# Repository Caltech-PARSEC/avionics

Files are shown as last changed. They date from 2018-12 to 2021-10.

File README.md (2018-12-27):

# Avionics

This repo is meant to contain the code for the microcontrollers on each board
and the Altium Designer files associated with the design of each board. When
adding your own stuff, try to stick with the folder naming convention and
structure seen here.

## Libraries
The libraries with the 'PARSEC' file name contain components that are generally
shared across the boards. If you need to add components for a project, add
them in a separate library file and add that file to the 'libraries' directory.

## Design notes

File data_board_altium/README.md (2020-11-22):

This folder is for Altium files for the on-rocket and ground station data boards.

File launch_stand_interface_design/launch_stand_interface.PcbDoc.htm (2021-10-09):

Reporting Options

# File in Previous Format

Date | : | 10/9/2021
Time | : | 3:20:03 PM
Filename | : | C:\Users\rayw1\Documents\GitHub\parsec_avionics\launch_stand_interface_design\launch_stand_interface.PcbDoc

Version | Warning

This file was generated by an earlier version of the software

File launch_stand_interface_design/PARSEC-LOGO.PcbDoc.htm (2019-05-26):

Reporting Options

# File in Previous Format

Date | : | 5/26/2019
Time | : | 2:11:39 AM
Filename | : | C:\Users\julli\OneDrive - California Institute of Technology\PARSEC\avionics\launch_stand_interface_design\PARSEC-LOGO.PcbDoc

Version | Warning

This file was generated by an earlier version of the software

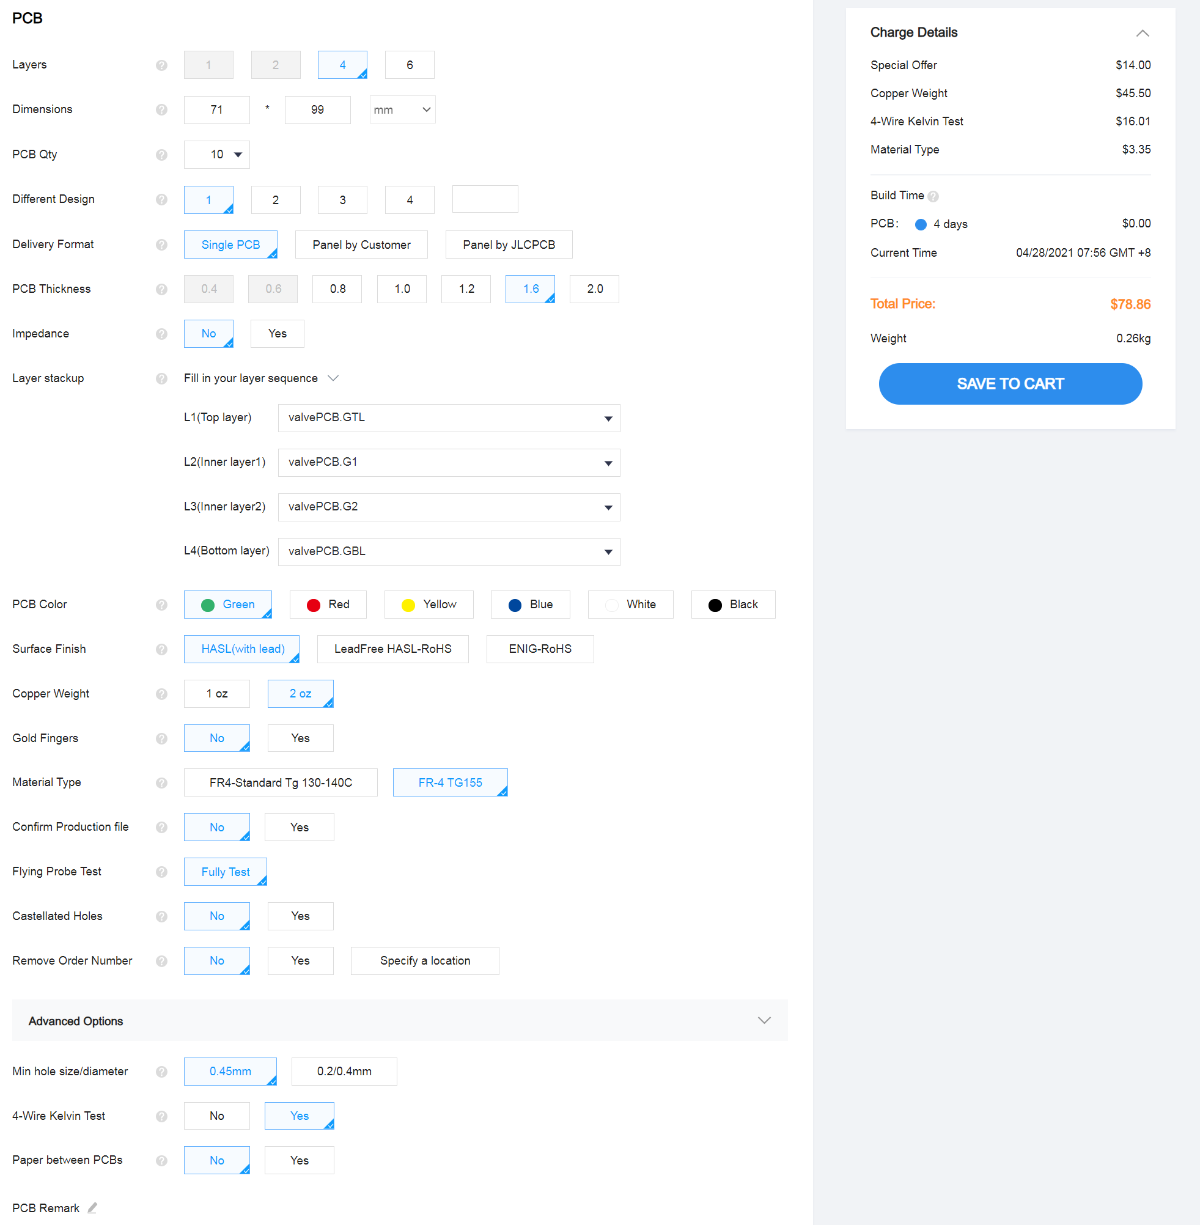
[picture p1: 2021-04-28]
valves/prop_valve_driver/valves_v2/JLCPCB_quote.PNG

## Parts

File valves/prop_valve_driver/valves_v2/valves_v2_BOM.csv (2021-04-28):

Comment | Description | Designator | Footprint | LibRef | Quantity | Value | Rating
CapCer | SMD Ceramic Capacitor | C1, C15, C16 | C0805_med_density | CapCer | 3 | 100n | 6.3V
CapTant | Through-hole tantalum capacitor | C2, C3, C4, C5 | C1206_tant_low_density | CapTant | 4 | 1u | 50V
CapCer | SMD Ceramic Capacitor | C6 | C0603_med_density | CapCer | 1 | 4u7 | 6.3V
CapCer | SMD Ceramic Capacitor | C7, C8, C10_FirstValve, C10_ThirdValve | C0603_med_density | CapCer | 4 | 100n | 6.3V
CapCer | SMD Ceramic Capacitor | C9 | C0603_med_density | CapCer | 1 | 10n | 6.3V
CapCer | SMD Ceramic Capacitor | C11, C12, C13, C14 | C0805_med_density | CapCer | 4 | 470n | 6.3V
CapCer | SMD Ceramic Capacitor | C17 | C0603_med_density | CapCer | 1 | 1u | 6.3V
1655-1921-1-ND | Schottky Diode | D1_FirstValve, D1_ThirdValve | DO-201AD | DiodeSchottky | 2
LED | Light-emitting diode | D2 | LED0805 | LED | 1 | Red
LED | Light-emitting diode | D3 | LED0805 | LED | 1 | Green
LED | Light-emitting diode | D4, D5 | LED0805 | LED | 2 | Blue
Molex KK 1x4 | 1x4 Molex KK Connector (CAN) | J1, J3 | Molex KK 4x1 | Molex KK 1x4 | 2
Battery | Molex 1x4 11A Connector | J2 | CON_2074781004_MOL | 2074781004 | 1
Header 4 | Header, 4-Pin | J4 | HDR1X4 | Header 4 | 1
Valve |  | J5_FirstValve, J5_ThirdValve | MOLEX_436500200 - duplicate | General Molex | 2
2STBN15D100 | 2STBN15D100 BJT | Q1_FirstValve, Q1_ThirdValve | D2PAK | BJT | 2
RK7002BMT116 | n-channel MOSEFT | Q2_FirstValve, Q2_ThirdValve | TRANS_RK7002BMHZG_ROM | RK7002BMT116 | 2
ResChip | SMD Chip resistor | R1 | R0805_med_density | ResChip | 1 | 120R
ResChip | SMD Chip resistor | R2 | R0805_med_density | ResChip | 1 | 100R
ResChip | SMD Chip resistor | R3_FirstValve, R3_ThirdValve | R1210_med_density | ResChip | 2 | 4m | 0.5W
ResChip | SMD Chip resistor | R4_FirstValve, R4_ThirdValve | R0603_med_density | ResChip | 2 | 91R | 0.25 W
ResChip | SMD Chip resistor | R5_FirstValve, R5_ThirdValve | R0603_med_density | ResChip | 2 | 10k
ResChip | SMD Chip resistor | R6_FirstValve, R6_ThirdValve | R0603_med_density | ResChip | 2 | 100R
ResChip | SMD Chip resistor | R7, R11 | R0805_med_density | ResChip | 2 | 240R
ResChip | SMD Chip resistor | R8 | R0805_med_density | ResChip | 1 | 412R
ResChip | SMD Chip resistor | R9, R15 | R0805_med_density | ResChip | 2 | 10R
ResChip | SMD Chip resistor | R12 | R0805_med_density | ResChip | 1 | 390R
ResChip | SMD Chip resistor | R13 | R0603_med_density | ResChip | 1 | 130R
ResChip | SMD Chip resistor | R14 | R0603_med_density | ResChip | 1 | 81R
ResChip | SMD Chip resistor | R16, R17, R18, R19 | R0805_med_density | ResChip | 4 | 100k
Switch | Push button switch, momentary, normally open | SW1, SW2, SW3, SW4, SW5 | PUSHBUTTON | Switch | 5
TCAN332DCNT | IC TXRX CAN 3.3V SOT23-8 | U1 | SOT-23-8 | TCAN332DCNT | 1
STM32F042K6T6 | STM32 MCU | U2 | LQFP-32 | STM32F042K6T6 | 1
INA240A3D | SchLib for TI op amp for current sensing. | U3_FirstValve, U3_ThirdValve | INA240A3D | INA240A3D | 2
LM317 | Linear Voltage Regulator | U4, U5 | D-PAK | LM317 | 2
SN74LVC14ADBR | Hex Schmitt-Trigger Inverter, DB0014A, LARGE T&R | U6 | SOP-14 | SN74LVC14 | 1 |  | Catalog
CSTCE8M00 | 8MHz Ceramic Resonator | Y1 | 8MHz Ceramic Resonator | CSTCE8M00 | 1

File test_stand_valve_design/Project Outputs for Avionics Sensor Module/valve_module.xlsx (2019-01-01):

Comment | Description | Designator | Footprint | LibRef | Quantity
1uF | 0805 Capacitor | C1, C22 | C0805 | C0805 | 2
0.1uF | 0805 Capacitor | C2, C23 | C0805 | C0805 | 2
100n | 0603 Capacitor | C3 | C0603 | C0603 | 1
1u | 0603 Capacitor | C4 | C0603 | C0603 | 1
100n | 0805 Capacitor | C5, C6, C7, C8, C10, C11, C12, C13, C14, C15, C16, C17 | C0805 | C0805 | 12
4u7 | 0805 Capacitor | C9 | C0805 | C0805 | 1
2u2 | 0603 Capacitor | C18, C19 | C0603 | C0603 | 2
1 uF | 0603 Capacitor | C20_VD1, C20_VD2, C20_VD3, C20_VD4, C20_VD5, C21_VD1, C21_VD2, C21_VD3, C21_VD4, C21_VD5 | C0603 | C0603 | 10
824501141 | TVS DIODE 14V 23.2V DO214AC | D1_VD1, D1_VD2, D1_VD3, D1_VD4, D1_VD5, D2_VD1, D2_VD2, D2_VD3, D2_VD4, D2_VD5 | DIODE-SMA | 824501141 | 10
LED | LED | D3 | 0805LED | LED | 1
FERRITE | FERRITE BEAD 0805 | FB1, FB2 | R0805 | FERRITE | 2
Molex KK 1x2 | 1x2 Molex KK Connector | P1, P2, P4_VD1, P4_VD2, P4_VD3, P4_VD4, P4_VD5, P5_VD1, P5_VD2, P5_VD3, P5_VD4, P5_VD5, P6 | Molex KK 2x1 | Molex KK 1x2 | 13
Molex KK 1x4 | 1x4 Molex KK Connector | P3, P7, P8, P9, P10, P11, P12, P13, P14, P15, P16 | Molex KK 4x1 | Molex KK 1x4 | 11
240R | RESISTOR 0805 | R1, R5 | R0805 | R0805 | 2
390R | RESISTOR 0805 | R2 | R0805 | R0805 | 1
100 | RESISTOR 0805 | R3 | R0805 | R0805 | 1
1k | RESISTOR 0805 | R4 | R0805 | R0805 | 1
536R | RESISTOR 0805 | R6 | R0805 | R0805 | 1
2k | RESISTOR 0805 | R7 | R0805 | R0805 | 1
Tactile Switch | TL3301AF160QG | SW1 | Tactile Switch | Tactile Switch | 1
LM317 | Linear Voltage Regulator | U1, U4 | D-PAK | LM317 | 2
MC-ARM-STM32F446-LQFP100 |  | U2 | STM-LQFP100_N | MC-ARM-STM32F446-LQFP100 | 1
 | Imported | U3_VD1, U3_VD2, U3_VD3, U3_VD4, U3_VD5 | PowerSO-20 | L298P013TR | 5
CSTCE8M00 | 8MHz Ceramic Resonator | Y1 | 8MHz Ceramic Resonator | CSTCE8M00 | 1

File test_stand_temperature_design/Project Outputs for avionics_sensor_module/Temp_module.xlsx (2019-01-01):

Comment | Description | Designator | Footprint | LibRef | Quantity
.1uF | 0805 Capacitor | C1 | C0805 | C0805 | 1
1uF | 0805 Capacitor | C2 | C0805 | C0805 | 1
100n | 0805 Capacitor | C3, C5, C6, C7, C8, C10, C11, C12, C13, C14, C15, C16, C17 | C0805 | C0805 | 13
1u | 0805 Capacitor | C4 | C0805 | C0805 | 1
4u7 | 0805 Capacitor | C9 | C0805 | C0805 | 1
2u2 | 0805 Capacitor | C18, C19 | C0805 | C0805 | 2
0.01uF | 0805 Capacitor | C20_TEMP1, C20_TEMP2, C20_TEMP3, C20_TEMP4, C20_TEMP5, C20_TEMP6, C20_TEMP7, C20_TEMP8, C20_TEMP9, C20_TEMP10, C22_TEMP1, C22_TEMP2, C22_TEMP3, C22_TEMP4, C22_TEMP5, C22_TEMP6, C22_TEMP7, C22_TEMP8, C22_TEMP9, C22_TEMP10 | C0805 | C0805 | 20
0.1uF | 0805 Capacitor | C21_TEMP1, C21_TEMP2, C21_TEMP3, C21_TEMP4, C21_TEMP5, C21_TEMP6, C21_TEMP7, C21_TEMP8, C21_TEMP9, C21_TEMP10, C23_TEMP1, C23_TEMP2, C23_TEMP3, C23_TEMP4, C23_TEMP5, C23_TEMP6, C23_TEMP7, C23_TEMP8, C23_TEMP9, C23_TEMP10, C24_TEMP1, C24_TEMP2, C24_TEMP3, C24_TEMP4, C24_TEMP5, C24_TEMP6, C24_TEMP7, C24_TEMP8, C24_TEMP9, C24_TEMP10 | C0805 | C0805 | 30
LED | LED | D1 | 0805LED | LED | 1
FERRITE | FERRITE BEAD 0805 | FB1, FB2 | R0805 | FERRITE | 2
PCC-SMP | THERMOCOUPLE CONNECTOR | J1_TEMP1, J1_TEMP2, J1_TEMP3, J1_TEMP4, J1_TEMP5, J1_TEMP6, J1_TEMP7, J1_TEMP8, J1_TEMP9, J1_TEMP10 | PCC-SMP | PCC-SMP | 10
Molex KK 1x2 | 1x2 Molex KK Connector | P1, P2 | Molex KK 2x1 | Molex KK 1x2 | 2
Header 4 | Header, 4-Pin | P3 | HDR1X4 | Header 4 | 1
240R | RESISTOR 0805 | R1 | R0805 | R0805 | 1
390 R | RESISTOR 0805 | R2 | R0805 | R0805 | 1
100R | RESISTOR 0805 | R3 | R0805 | R0805 | 1
1K | RESISTOR 0805 | R4 | R0805 | R0805 | 1
2k | RESISTOR 0805 | R5 | R0805 | R0805 | 1
Push Switch |  | SW1 | PUSHBUTTON | PUSHBUTTON | 1
LM317 | Linear Voltage Regulator | U1 | D-PAK | LM317 | 1
MC-ARM-STM32F446-LQFP100 |  | U2 | STM-LQFP100_N | MC-ARM-STM32F446-LQFP100 | 1
MAXIM TSSOP14 |  | U3_TEMP1, U3_TEMP2, U3_TEMP3, U3_TEMP4, U3_TEMP5, U3_TEMP6, U3_TEMP7, U3_TEMP8, U3_TEMP9, U3_TEMP10 | MAXIM TSSOP14 | MAXIM TSSOP14 | 10
CSTCE8M00 | 8MHz Ceramic Resonator | Y1 | 8MHz Ceramic Resonator | CSTCE8M00 | 1

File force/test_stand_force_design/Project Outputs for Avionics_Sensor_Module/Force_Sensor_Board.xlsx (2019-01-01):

Comment | Description | Designator | Footprint | LibRef | Quantity
0.1uF | 0805 Capacitor | C1, C5, C21_PA1, C21_PA2, C21_PA3 | C0805 | C0805 | 5
1uF | 0805 Capacitor | C2 | C0805 | C0805 | 1
100n | 0805 Capacitor | C3, C6, C7, C8, C9, C11, C12, C13, C14, C15, C16, C17, C18 | C0805 | C0805 | 13
1u | 0805 Capacitor | C4 | C0805 | C0805 | 1
4u7 | 0805 Capacitor | C10 | C0805 | C0805 | 1
 | 0805 Capacitor | C19, C20 | C0805 | C0805 | 2
BAT54-SOT23 | SINGLE SHOTTKY DIODE | D1_PA1, D1_PA2, D1_PA3 | SOT23-DIODE | BAT54-SOT23 | 3
LED | LED | D2 | 0805LED | LED | 1
FERRITE | FERRITE BEAD 0805 | FB1, FB2 | R0805 | FERRITE | 2
 | RESISTOR 0603 | Load_PA1, Load_PA2, Load_PA3 | R0603 | R0603 | 3
Molex KK 1x2 | 1x2 Molex KK Connector | P1, P2 | Molex KK 2x1 | Molex KK 1x2 | 2
Molex KK 1x4 | 1x4 Molex KK Connector | P3, P4, P5, P6, P8 | Molex KK 4x1 | Molex KK 1x4 | 5
Header 4 | Header, 4-Pin | P7 | HDR1X4 | Header 4 | 1
240R | RESISTOR 0805 | R1 | R0805 | R0805 | 1
5.6k | RESISTOR 0805 | R1_PA1, R1_PA2, R1_PA3 | R0805 | R0805 | 3
390R | RESISTOR 0805 | R2 | R0805 | R0805 | 1
1k | RESISTOR 0805 | R2_PA1, R2_PA2, R2_PA3, R5 | R0805 | R0805 | 4
120R | RESISTOR 0805 | R3 | R0805 | R0805 | 1
100R | RESISTOR 0805 | R4 | R0805 | R0805 | 1
10k | RESISTOR 0805 | R6_PA1, R6_PA2, R6_PA3 | R0805 | R0805 | 3
2k | RESISTOR 0805 | R7 | R0805 | R0805 | 1
1k3 | RESISTOR 0603 | Rg_PA1, Rg_PA2, Rg_PA3 | R0603 | R0603 | 3
Push Switch |  | SW1 | PUSHBUTTON | PUSHBUTTON | 1
LM317 | Linear Voltage Regulator | U1 | D-PAK | LM317 | 1
MC-ARM-STM32F446-LQFP100 |  | U2 | STM-LQFP100_N | MC-ARM-STM32F446-LQFP100 | 1
TCAN332DCNT | IC TXRX CAN 3.3V SOT23-8 | U3 | SOT-23-8 | TCAN332DCNT | 1
INA125_D_16 | Imported | U4_PA1, U4_PA2, U4_PA3 | D16 | INA125_D_16 | 3
CSTCE8M00 | 8MHz Ceramic Resonator | Y1 | 8MHz Ceramic Resonator | CSTCE8M00 | 1

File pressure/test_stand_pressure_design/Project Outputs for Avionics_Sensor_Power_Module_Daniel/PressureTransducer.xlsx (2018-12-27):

Comment | Description | Designator | Footprint | LibRef | Quantity
1.0uF | 0805 Capacitor | C1 | C0805 | C0805 | 1
0.1uF | 0805 Capacitor | C2 | C0805 | C0805 | 1
100n | 0805 Capacitor | C3, C4, C6, C7, C8, C9, C12, C13, C14, C15, C17, C18, C19, C20 | C0805 | C0805 | 14
1u | 0805 Capacitor | C5 | C0805 | C0805 | 1
4u7 | 0805 Capacitor | C10 | C0805 | C0805 | 1
2u2 | 0805 Capacitor | C11, C16 | C0805 | C0805 | 2
LED | LED | D1 | 0805LED | LED | 1
FERRITE | FERRITE BEAD 0805 | FB1, FB2 | R0805 | FERRITE | 2
Molex KK 1x2 | 1x2 Molex KK Connector | P1, P2 | Molex KK 2x1 | Molex KK 1x2 | 2
Molex KK 1x4 | 1x4 Molex KK Connector | P3, P4, P6_PT1, P6_PT2, P6_PT3, P6_PT4, P6_PT5, P6_PT6, P6_PT7, P6_PT8, P6_PT9 | Molex KK 4x1 | Molex KK 1x4 | 11
Header 4 | Header, 4-Pin | P5 | HDR1X4 | Header 4 | 1
240R | RESISTOR 0805 | R1, R6_PT1, R6_PT2, R6_PT3, R6_PT4, R6_PT5, R6_PT6, R6_PT7, R6_PT8, R6_PT9 | R0805 | R0805 | 10
390R | RESISTOR 0805 | R2 | R0805 | R0805 | 1
120R | RESISTOR 0805 | R3 | R0805 | R0805 | 1
100R | RESISTOR 0805 | R4 | R0805 | R0805 | 1
1k | RESISTOR 0805 | R5, R8 | R0805 | R0805 | 2
464R | RESISTOR 0805 | R7_PT1, R7_PT2, R7_PT3, R7_PT4, R7_PT5, R7_PT6, R7_PT7, R7_PT8, R7_PT9 | R0805 | R0805 | 9
Push Switch |  | SW1 | PUSHBUTTON | PUSHBUTTON | 1
LM317 | Linear Voltage Regulator | U1 | D-PAK | LM317 | 1
TCAN332DCNT | IC TXRX CAN 3.3V SOT23-8 | U2 | SOT-23-8 | TCAN332DCNT | 1
MC-ARM-STM32F446-LQFP100 |  | U3 | STM-LQFP100_N | MC-ARM-STM32F446-LQFP100 | 1
CSTCE8M00 | 8MHz Ceramic Resonator | Y1 | 8MHz Ceramic Resonator | CSTCE8M00 | 1

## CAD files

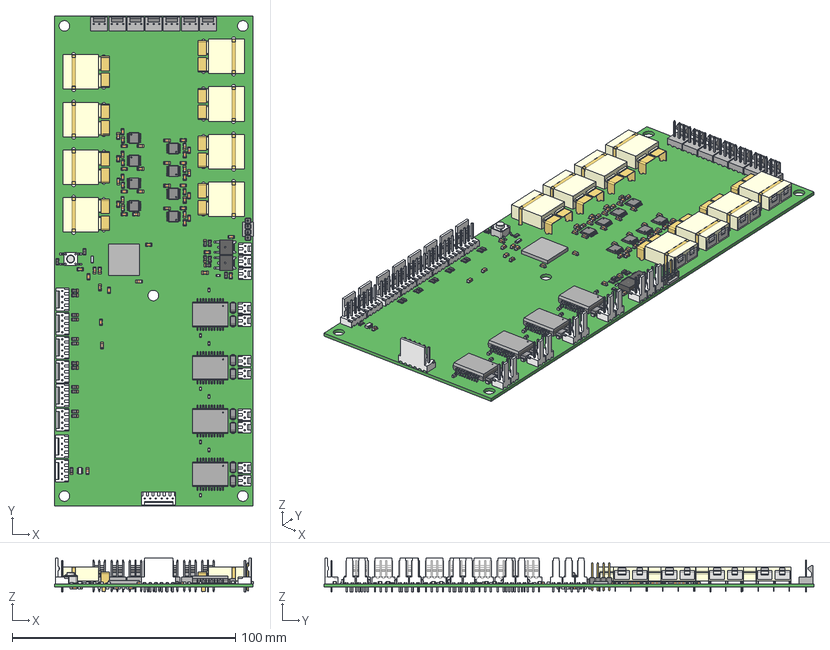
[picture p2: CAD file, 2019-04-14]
rocket_main/rocket_main.step
89.2 x 219.7 x 15.2 mm
Extruded x 30
User_Library-cap0805_pad_0805___ x 75
User_Library-cap0805_cap0805_body___ x 75
User_Library-Molex_-_3-Pin_Header_with_Lock_(0.100in_pitch)_Molex_-_ 3-Pin_Header_Base_with_Lock_(0.100in_pitch) x 7
User_Library-Molex_-_3-Pin_Header_with_Lock_(0.100in_pitch)_Molex_-_ Header_Pin x 21
User_Library-molex_kk_0_1in_latching_4_way_vertical_header x 8
User_Library-molex_kk_0_1in_latching_6_way_vertical_header
User_Library-TO252AA x 2
User_Library-res0805_pad_0805___ x 21
User_Library-res0805_res0805_body___ x 21
User_Library-molex_kk_0_1in_latching_2_way_vertical_header x 11
User_Library-LED_SMD0805
PowerSO-20 x 4
Thermocouple-PCC-SMP x 8
User_Library-DO-214Aa_SMA x 8
TSSOP14 x 8
CSTCE
User_Library-SOT23-8
TL1105CONTACTDOME
TL3301GBODY
TL1105COVER
TL1105-3301ACTUATOR_A_5

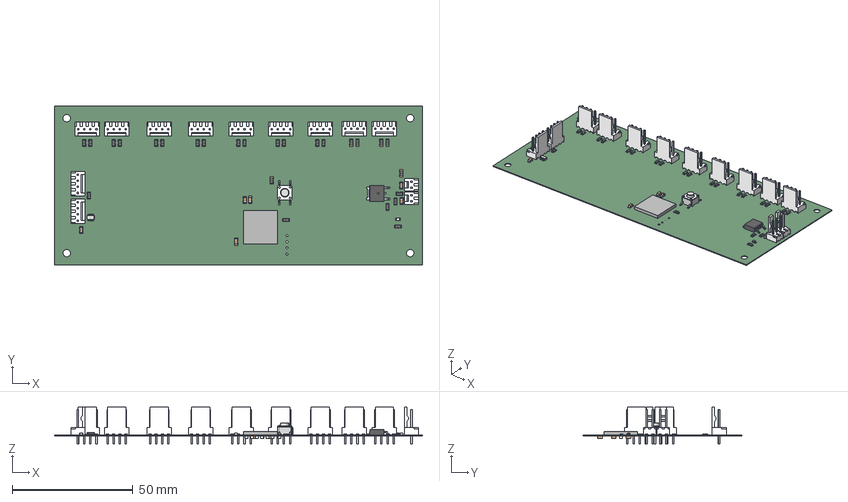
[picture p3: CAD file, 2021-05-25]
pressure/test_stand_pressure_design/PressureTransducer.step
152.4 x 65.9 x 15.2 mm
User_Library-res0805_pad_0805___ x 26
User_Library-res0805_res0805_body___ x 26
User_Library-LED_SMD0805
Extruded
User_Library-SOT23-8
User_Library-TO252AA
TL1105CONTACTDOME
TL3301GBODY
TL1105COVER
TL1105-3301ACTUATOR_A_5
User_Library-molex_kk_0_1in_latching_4_way_vertical_header x 11
User_Library-molex_kk_0_1in_latching_2_way_vertical_header x 2
User_Library-cap0805_pad_0805___ x 20
User_Library-cap0805_cap0805_body___ x 20

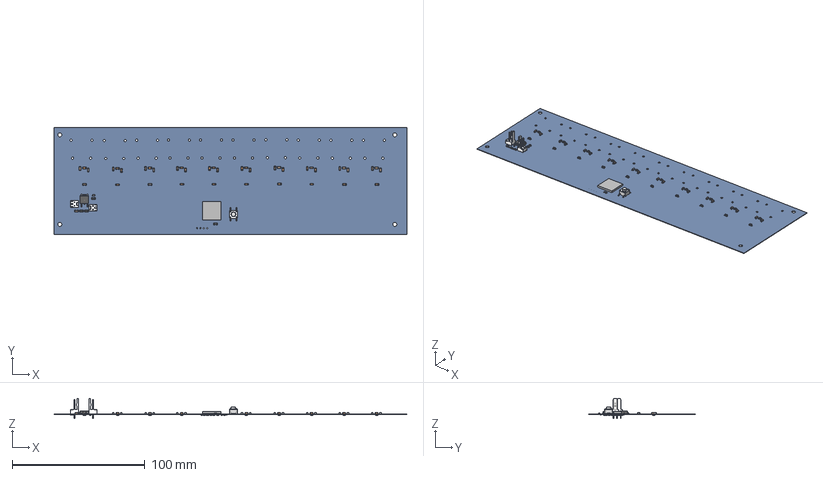
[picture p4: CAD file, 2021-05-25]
test_stand_temperature_design/Temp_module.step
266.1 x 80.4 x 15.2 mm
User_Library-res0805_pad_0805___ x 7
User_Library-res0805_res0805_body___ x 7
User_Library-LED_SMD0805
User_Library-cap0805_pad_0805___ x 69
User_Library-cap0805_cap0805_body___ x 69
User_Library-molex_kk_0_1in_latching_2_way_vertical_header x 2
User_Library-TO252AA
Extruded
TL1105CONTACTDOME
TL3301GBODY
TL1105COVER
TL1105-3301ACTUATOR_A_5

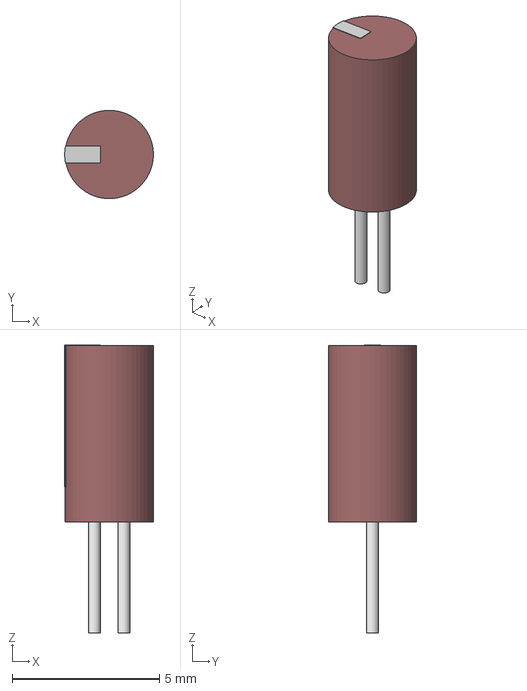
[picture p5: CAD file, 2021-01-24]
valves/prop_valve_driver/valves_v2/Models/CAP_UMA_3X5_NCH.step
3.01 x 3.00 x 9.77 mm

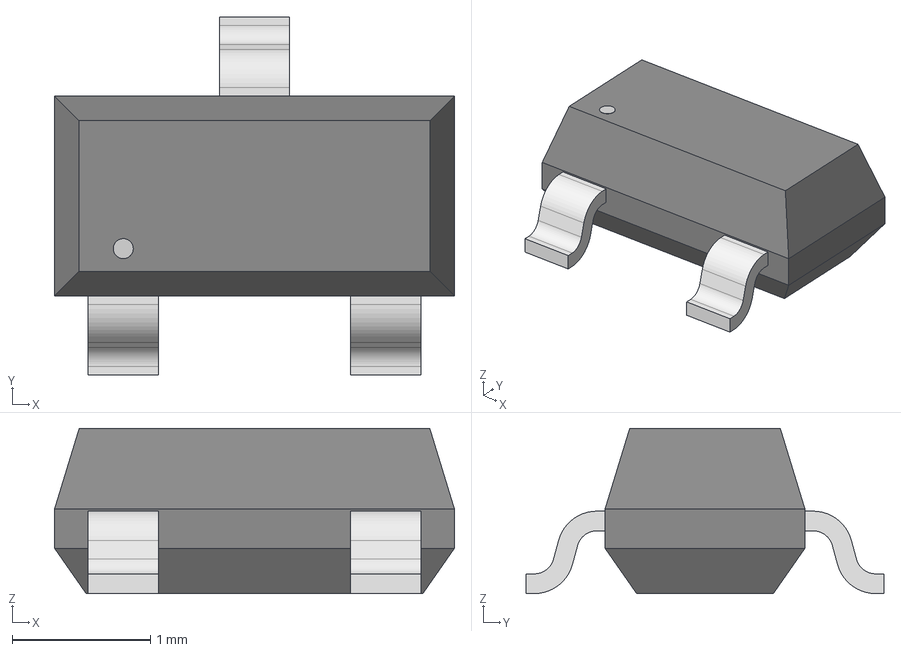
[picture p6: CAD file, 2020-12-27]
valves/prop_valve_driver/valves_v2/Models/TRANS_RK7002BMHZG_ROM.step
2.90 x 2.59 x 1.20 mm

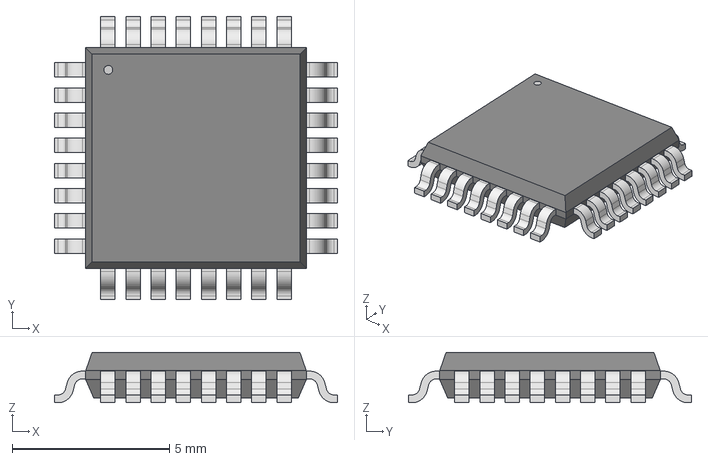
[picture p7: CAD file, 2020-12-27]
valves/prop_valve_driver/valves_v2/Models/LQFP-32.step
8.99 x 8.99 x 1.60 mm

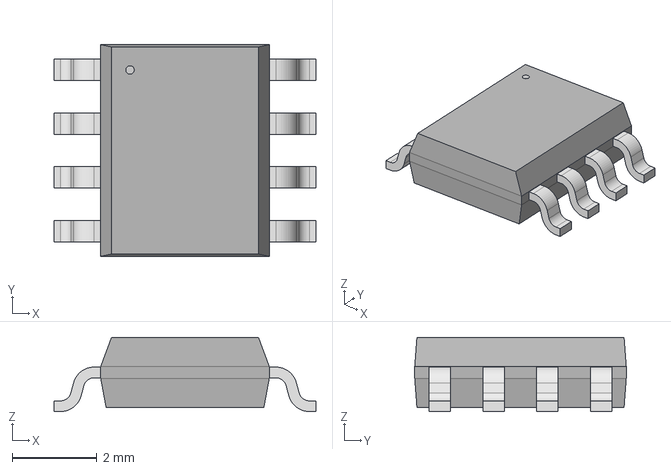
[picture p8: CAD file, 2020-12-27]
valves/prop_valve_driver/valves_v2/Models/D8_TEX-M.step
6.20 x 5.00 x 1.75 mm

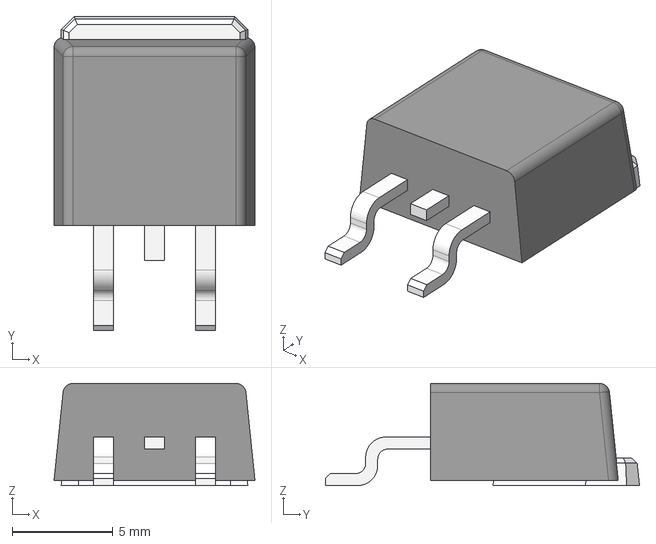
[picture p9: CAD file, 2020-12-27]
valves/prop_valve_driver/valves_v2/Models/D2PAK-2 L7805.step
10.0 x 15.6 x 5.08 mm

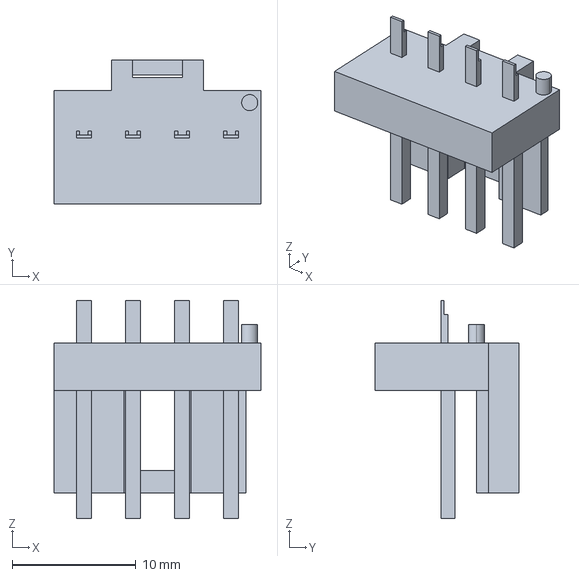
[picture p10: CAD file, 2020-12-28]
valves/prop_valve_driver/valves_v2/Models/2074781004.stp
16.7 x 11.6 x 17.6 mm

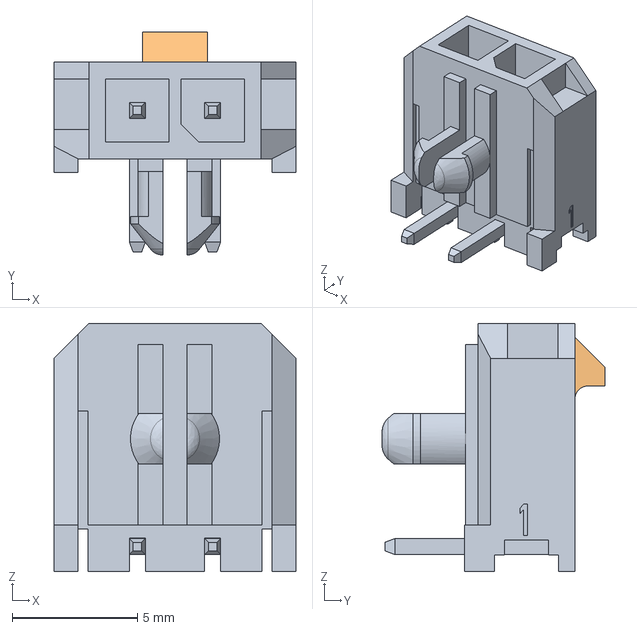
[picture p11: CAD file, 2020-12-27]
valves/prop_valve_driver/valves_v2/Models/436500200.stp
9.65 x 8.91 x 9.90 mm

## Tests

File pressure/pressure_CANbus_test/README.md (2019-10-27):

# Pressure CAN bus test
This code is designed to run a simple test of the ability of the pressure
boards to send and recieve CAN messages. When wired as described below,
pushing the button connected to one board will cause its LED to change, and
will cause it to send a CAN message to the other board instructing it to
set its LED to the opposite state of the original board's LED.

## Wiring
Pin header P6_PT9 connect to push button. Voltage should be normally 5V.
Pin header P6_PT5 connect to LED through ~100 ohm resistor.
The pin to use on each header is the one connected to R7_PTx.
Connect the CANH and CANL pins of the two pressure boards together.

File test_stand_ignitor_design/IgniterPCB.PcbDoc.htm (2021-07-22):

Reporting Options

# File in Previous Format

Date | : | 6/4/2021
Time | : | 3:36:19 AM
Filename | : | C:\Users\rayw1\Documents\GitHub\parsec_avionics\test_stand_ignitor_design\IgniterPCB.PcbDoc

Version | Warning

This file was generated by an earlier version of the software

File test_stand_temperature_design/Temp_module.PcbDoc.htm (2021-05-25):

Reporting Options

# File in Previous Format

Date | : | 5/25/2021
Time | : | 12:05:54 PM
Filename | : | C:\Users\julli\OneDrive - California Institute of Technology\PARSEC\avionics\test_stand_temperature_design\Temp_module.PcbDoc

Version | Warning

This file was generated by an earlier version of the software

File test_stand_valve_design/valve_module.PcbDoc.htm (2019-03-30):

Reporting Options

# File in Previous Format

Date | : | 3/29/2019
Time | : | 3:01:08 PM
Filename | : | C:\Users\julli\OneDrive - California Institute of Technology\PARSEC\avionics\test_stand_valve_design\valve_module.PcbDoc

Version | Warning

This file was generated by an earlier version of the software

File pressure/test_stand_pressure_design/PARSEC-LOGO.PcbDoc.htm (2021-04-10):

Reporting Options

# File in Previous Format

Date | : | 4/10/2021
Time | : | 6:36:28 PM
Filename | : | C:\Users\loren\Documents\Projects\PARSEC Electrical\avionics\pressure\test_stand_pressure_design\PARSEC-LOGO.PcbDoc

Version | Warning

This file was generated by an earlier version of the software

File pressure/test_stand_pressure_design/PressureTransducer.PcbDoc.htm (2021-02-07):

Reporting Options

# File in Previous Format

Date | : | 2/6/2021
Time | : | 9:37:24 PM
Filename | : | C:\Users\loren\Documents\Projects\PARSEC Electrical\avionics\pressure\test_stand_pressure_design\PressureTransducer.PcbDoc

Version | Warning

This file was generated by an earlier version of the software

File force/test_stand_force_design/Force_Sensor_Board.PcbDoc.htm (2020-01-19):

Reporting Options

# File in Previous Format

Date | : | 1/26/2019
Time | : | 7:23:34 PM
Filename | : | C:\Users\julli\OneDrive - California Institute of Technology\PARSEC\avionics\test_stand_force_design\Force_Sensor_Board.PcbDoc

Version | Warning

This file was generated by an earlier version of the software

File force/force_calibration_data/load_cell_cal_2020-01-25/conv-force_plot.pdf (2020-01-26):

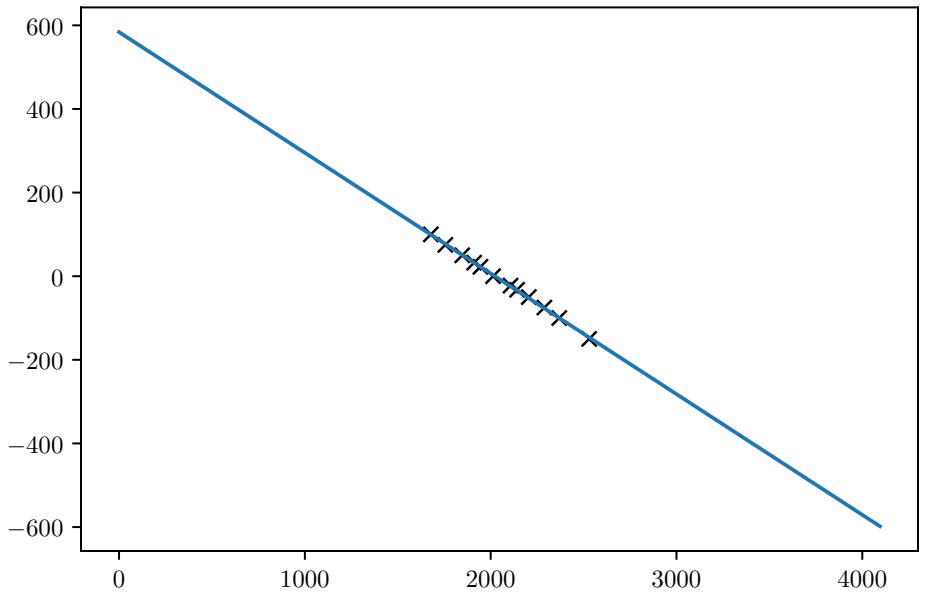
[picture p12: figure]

### ADC Conversion

### Pounds of compressive force

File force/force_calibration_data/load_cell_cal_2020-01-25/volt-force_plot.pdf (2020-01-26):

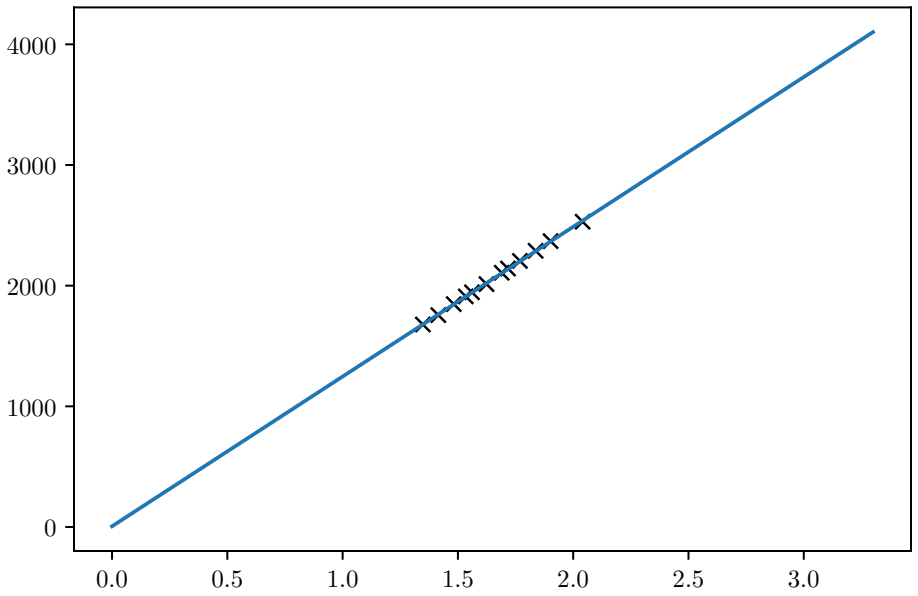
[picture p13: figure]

### Voltage (V)

### ADC Conversion value

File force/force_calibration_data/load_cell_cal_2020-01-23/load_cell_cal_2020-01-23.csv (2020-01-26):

Load Cell S/N | Port No. | Direction | Force (lbs) | ADC Conv.
1818000262 | 1 |  | 0 | 2041
1818000254 | 2 |  | 0 | 2018
1818000259 | 3 |  | 0 | 2041
1818000262 | 1 |  | 0 | 2033
1818000254 | 3 |  | 0 | 2031
1818000259 | 2 |  | 0 | 2030
1818000262 | 1 | Tension | 50 | 2045
1818000254 | 3 | Tension | 50 | 2192
1818000259 | 2 | Tension | 50 | 2202
1818000262 | 1 | Tension | 100 | 2066
1818000254 | 3 | Tension | 100 | 2367
1818000259 | 2 | Tension | 100 | 2378
1818000254 | 3 | Tension | 150 | 2544
1818000259 | 2 | Tension | 150 | 2532
1818000262 | 2 | Tension | 100 | 2374
1818000262 | 2 | Tension | 150 | 2530
1818000262 | 2 | Tension | 50 | 2195
1818000262 | 2 | Compression | 45 | 1959
1818000262 | 2 | Compression | 90 | 1959
1818000254 | 3 | Compression | 90 | 1965
1818000254 | 3 | Compression | 45 | 1963
1818000259 | 1 | Compression | 90 | 2011

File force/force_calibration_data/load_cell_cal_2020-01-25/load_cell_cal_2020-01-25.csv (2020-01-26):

Load Cell S/N | Port No. | Direction | Force (lbs) | ADC Conv. | Voltage (V)
1818000262 | 1 |  | 0 | 2013 | 1.624
1818000254 | 2 |  | 0 | 2002 | 1.62
1818000259 | 3 |  | 0 | 2044 | 1.646
1818000262 | 1 | Tension | 22.5 | 2107 | 1.69
1818000262 | 1 | Tension | 32.5 | 2142 | 1.717
1818000262 | 1 | Tension | 50 | 2205 | 1.769
1818000262 | 1 | Tension | 75 | 2289 | 1.837
1818000262 | 1 | Tension | 100 | 2369 | 1.902
1818000262 | 1 | Tension | 150 | 2530 | 2.041
1818000262 | 1 | Compression | 22.5 | 1945 | 1.561
1818000262 | 1 | Compression | 32.5 | 1911 | 1.534
1818000262 | 1 | Compression | 50 | 1847 | 1.482
1818000262 | 1 | Compression | 75 | 1756 | 1.415
1818000262 | 1 | Compression | 100 | 1678 | 1.348
1818000254 | 2 | Compression | 22.5 | 1923
1818000254 | 2 | Compression | 32.5 | 1900
1818000254 | 2 | Compression | 50 | 1827
1818000254 | 2 | Compression | 75 | 1749
1818000254 | 2 | Compression | 100 | 1661
1818000259 | 3 | Compression | 22.5 | 1963
1818000259 | 3 | Compression | 32.5 | 1921
1818000259 | 3 | Compression | 50 | 1869
1818000259 | 3 | Compression | 75 | 1774
1818000259 | 3 | Compression | 100 | 1687
1818000254 | 1 | Compression | 22.5 | 1918
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

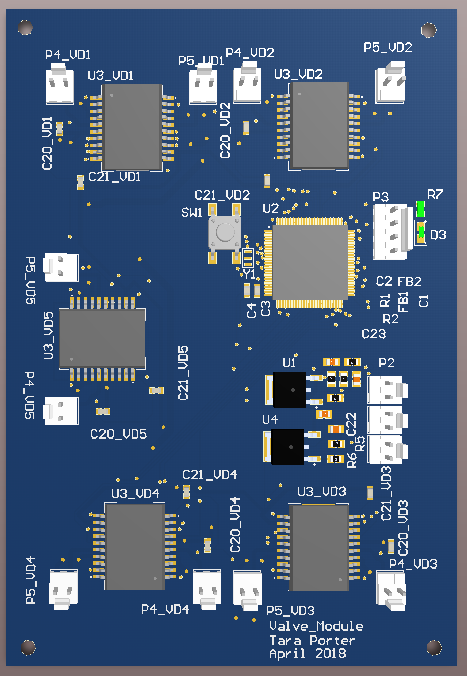
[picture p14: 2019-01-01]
test_stand_valve_design/valve pic.PNG

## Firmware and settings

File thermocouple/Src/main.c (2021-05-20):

/**
  ******************************************************************************
  * @file           : main.c
  * @brief          : Main program body
  ******************************************************************************
  ** This notice applies to any and all portions of this file
  * that are not between comment pairs USER CODE BEGIN and
  * USER CODE END. Other portions of this file, whether 
  * inserted by the user or by software development tools
  * are owned by their respective copyright owners.
  *
  * COPYRIGHT(c) 2021 STMicroelectronics
  *
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
  ******************************************************************************
  */
/* Includes ------------------------------------------------------------------*/
#include "main.h"
#include "stm32f4xx_hal.h"
#include "can.h"
#include "spi.h"
#include "tim.h"
#include "gpio.h"


/* USER CODE BEGIN PV */

/* USER CODE END PV */

void SystemClock_Config(void);

/* USER CODE BEGIN PFP */

/* USER CODE END PFP */

/* USER CODE BEGIN 0 */

// Structs for containing CAN message information
CAN_RxHeaderTypeDef baseCanRxHead;
CAN_TxHeaderTypeDef baseCanTxHead;

// The port number portion of the CAN ID corresponding to the message
// send for the data of each of the sensors, shifted so that the
// field is properly positioned within the CAN ID.
const int portNum[NUM_SENSORS] = {
    0 << PORT_NUM_SHIFT,
    1 << PORT_NUM_SHIFT,
    2 << PORT_NUM_SHIFT,
    3 << PORT_NUM_SHIFT,
    4 << PORT_NUM_SHIFT,
    5 << PORT_NUM_SHIFT,
    6 << PORT_NUM_SHIFT,
    7 << PORT_NUM_SHIFT,
    8 << PORT_NUM_SHIFT
};

// Expected to be used by the timer 3 ISR to determine which of the
// channels to average and send data for over the CAN bus.
//static int nextIdxToSend = 0;

// Chip select pins for each thermocouple
const uint16_t csPins[NUM_SENSORS] = {
  CS1_Pin, 
  CS2_Pin, 
  CS3_Pin, 
  CS4_Pin, 
  CS5_Pin, 
  CS6_Pin, 
  CS7_Pin, 
  CS8_Pin, 
  CS9_Pin, 
  CS10_Pin
};

// GPIO Port of each chip select pin
static GPIO_TypeDef* csPinPorts[NUM_SENSORS] = {
  CS1_GPIO_Port,
  CS2_GPIO_Port,
  CS3_GPIO_Port,
  CS4_GPIO_Port,
  CS5_GPIO_Port,
  CS6_GPIO_Port,
  CS7_GPIO_Port,
  CS8_GPIO_Port,
  CS9_GPIO_Port,
  CS10_GPIO_Port
};

// Buffer for each thermocouple's 3 byte reading
static uint8_t tempDataBuffer[NUM_SENSORS][3];
static uint8_t cjDataBuffer[2];
//static int tempDataReady[NUM_SENSORS] = {0, 0, 0, 0, 0, 0, 0, 0, 0, 0};


static uint8_t tempDataAddr[] = {0x0C};
static uint8_t cjDataAddr[] = {0x0A};
static uint8_t requestConv[2] = {0x80, 0b01000000};

// The number of thermocouple conversions triggered in
// the time it takes for a single conversion to complete.
// For a 660ms max conversion time, if we trigger a conversion
// every 100 ms, this value is ceiling(6.6) = 7
static int trigToReadGap = 7;

int trigInd = 0;
int readInd;

/* USER CODE END 0 */

/**
  * @brief  The application entry point.
  *
  * @retval None
  */
int main(void)
{
  /* MCU Configuration----------------------------------------------------------*/

  /* Reset of all peripherals, Initializes the Flash interface and the Systick. */
  HAL_Init();

  /* Configure the system clock */
  SystemClock_Config();

  /* Initialize all configured peripherals */
  MX_GPIO_Init();
  MX_CAN1_Init();
  MX_SPI1_Init();
  MX_TIM3_Init();

  /* USER CODE BEGIN 2 */
  // Start the IRQ timer on which data is sent over CAN
  HAL_TIM_Base_Start_IT(&htim3);


  // Initialize the CAN peripheral
  HAL_CAN_Init(&hcan1);

  // Configure CAN hardware receive filters
  //CAN_filterConfig();

  // Start the CAN module
  HAL_CAN_Start(&hcan1);


  // Start listening for CAN traffic on interrupt
  HAL_CAN_ActivateNotification(&hcan1, CAN_IT_RX_FIFO0_MSG_PENDING);

  // Set transmission parameters that are common to all Tx messages
  baseCanTxHead.IDE = CAN_ID_STD; // Standard 11-bit ID
  baseCanTxHead.StdId = OWN_CAN_ID; // CAN ID with port number = 0
  baseCanTxHead.RTR = CAN_RTR_DATA; // data frame (not a request frame)
  baseCanTxHead.DLC = 3;      // Number of data bytes


  // Just a buffer where AddTxMessage can return a code for which Tx
  // mailbox it added the message to. We don't care what it is.
  uint32_t mailbox;

  // Write all chip select pins low (inactive)
  for (int i = 0; i < NUM_SENSORS; i++)
  {
	  HAL_GPIO_WritePin(csPinPorts[i], csPins[i], 1);
  }

  // Initialize thermocouple signal processing ICs
  for (int i = 0; i < NUM_SENSORS; i++)
  {
	  // Write to configuration register 1 to average 16 samples per conversion,
	  // and ensure type K thermocouples are used.
	  uint8_t config1[2] = {0x81, 0b01110011};
	  HAL_GPIO_WritePin(csPinPorts[i], csPins[i], 0);
	  HAL_SPI_Transmit(&hspi1, (uint8_t *)config1, 2, HAL_MAX_DELAY);
	  HAL_GPIO_WritePin(csPinPorts[i], csPins[i], 1);
  }


  /* USER CODE END 2 */

  /* Infinite loop */
  /* USER CODE BEGIN WHILE */
  while (1)
  {

  /* USER CODE END WHILE */

  /* USER CODE BEGIN 3 */

  // Trigger a one-shot conversion to thermocouple number `trigInd`
  HAL_GPIO_WritePin(csPinPorts[trigInd], csPins[trigInd], 0);
  HAL_SPI_Transmit(&hspi1, (uint8_t *) requestConv, 2, HAL_MAX_DELAY);
  HAL_GPIO_WritePin(csPinPorts[trigInd], csPins[trigInd], 1);

  // Read the value from a previously triggered conversion on a
  // different thermocouple.
  readInd = (trigInd - trigToReadGap) % NUM_SENSORS;
  if (readInd < 0) {readInd += NUM_SENSORS;}

  HAL_GPIO_WritePin(csPinPorts[readInd], csPins[readInd], 0);
  HAL_SPI_Transmit(&hspi1, (uint8_t *) tempDataAddr, 1, HAL_MAX_DELAY);
  HAL_SPI_Receive(&hspi1, &tempDataBuffer[readInd][0], 3, HAL_MAX_DELAY);
  HAL_GPIO_WritePin(csPinPorts[readInd], csPins[readInd], 1);

  HAL_Delay(10);

  // For debugging, check what it's reading for cold junction temperature
  HAL_GPIO_WritePin(csPinPorts[readInd], csPins[readInd], 0);
  HAL_SPI_Transmit(&hspi1, (uint8_t *) cjDataAddr, 1, HAL_MAX_DELAY);
  HAL_SPI_Receive(&hspi1, (uint8_t *) cjDataBuffer, 2, HAL_MAX_DELAY);
  HAL_GPIO_WritePin(csPinPorts[readInd], csPins[readInd], 1);

  trigInd = (trigInd + 1) % NUM_SENSORS;


  int temp24 = tempDataBuffer[readInd][0] << 16 | \
                   tempDataBuffer[readInd][1] << 8 |  \
                   tempDataBuffer[readInd][2];

  int cjTemp = (cjDataBuffer[0] << 8) | cjDataBuffer[1];
  cjTemp = cjTemp & 0xFFFFFFFF;

//  if (temp24 & 0x800000)
//  {
//    temp24 |= 0xFF000000; //fix sign
//  }
//
//  temp24 >>= 5;
//
//  float tempfloat = temp24;
//  tempfloat *= 0.0078125;
//  tempfloat += 273.15;

  // Specify the contents of the message we're going to send.

  // Copy the base Tx message header into the header for this
  // message specifically.
  CAN_TxHeaderTypeDef msgCanTxHead =  baseCanTxHead;

  // Write the port ID for this sensor to the appropriate field
  // of the CAN ID.
  msgCanTxHead.StdId = OWN_CAN_ID | portNum[readInd];

  // Send the value for this sensor measurement over the CAN bus
  uint8_t canData[3];
  canData[2] = (temp24 >> 16) & 0xFF;
  canData[1] = (temp24 >> 8)  & 0xFF;
  canData[0] = temp24 & 0xFF;

  HAL_CAN_AddTxMessage(&hcan1, &msgCanTxHead, canData, &mailbox);

  HAL_Delay(100);


//  int sensorNum = 1;
///*    uint16_t msgID = create_ID(BOARD_ID, sensorNum);
//    can_msg_t msg;
//
//*/
//    uint16_t value = tempfloat*32;
///*    CAN_short_msg(&msg, msgID, value);
//
//    while(!CAN_can_transmit()){};
//
//    CAN_queue_transmit(&msg);
//
//*/
//    volatile int var = 0;
//
//  }
//  /* USER CODE END 3 */

  }
}

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


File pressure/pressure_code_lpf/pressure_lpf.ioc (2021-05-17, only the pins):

Mcu.UserName=STM32F446VETx
PA0-WKUP.Signal=ADCx_IN0
PA1.Signal=ADCx_IN1
PA11.Signal=CAN1_RX
PA12.Signal=CAN1_TX
PA13.Signal=SYS_JTMS-SWDIO
PA14.Signal=SYS_JTCK-SWCLK
PA2.Signal=ADCx_IN2
PA6.Signal=ADCx_IN6
PA7.Signal=ADCx_IN7
PC0.Signal=ADCx_IN10
PC1.Signal=ADCx_IN11
PC2.Signal=ADCx_IN12
PC4.Signal=ADCx_IN14
PH0-OSC_IN.Signal=RCC_OSC_IN
PH1-OSC_OUT.Signal=RCC_OSC_OUT

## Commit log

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2019-01-01 Added temperature sensor design and code and force sensor design.
    [Avionics_Sensor_Module.PrjPcb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]
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2019-02-09 Minor edits while looking around designs. The force code now records ADC status in a variable.
    [Avionics Sensor Module.PrjPcb, Force_Sensor_Board.PcbDoc, PressureTransducer.PcbDoc]
2019-02-15 The igniter board is now shrunk down to about 2.5 x 3 inches and all the design violations have been addressed. Also changed a parameter in the adc.c file of the force code to have NbrOfDiscConversio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
    [Force_Sensor_Board.PcbDoc, IgniterPCB.PcbDoc, igniter.PrjPcb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]
2019-03-26 main avionics pcb design
    laid out and routed everything for the rocket avionics board except IMU
    connector
    [Power.SchDoc, Power_Schematic.SchDoc, Pressure_Transducer.SchDoc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]
2019-03-27 Completed avionics board design
    Added CAN and IMU connectors, placed component labels, added mounting
    holes
    [imu.SchDoc, rocket_main.PcbDoc, rocket_main.PrjPcb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]
2019-03-28 Updated avionics board
    Added potentiometer connectors, caps on analog lines, and moved CAN chip
    [Power_Schematic.SchDoc, Pressure_Transducer.SchDoc, imu.SchDoc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]
2019-03-28 Converted board to 4 layers
    ground plane moved to 2nd layer, power traces moved to 3rd layer
    [Power_Schematic.SchDoc, Pressure_Transducer.SchDoc, Temp_converter.SchDoc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]
2019-03-29 changed STM coupling capacitors
    moved capacitors directly under STM32 and made connections from VDD pins
    to caps more direct; moved signals that were in the way
    [rocket_main.PcbDoc]
2019-03-29 fixed missing 12V connection
    [rocket_main.PcbDoc]
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2019-03-30 Revert "Messing about with the force board schematics"
    This reverts commit 2567c6b501821507388e7e40463a2e3277f00319.
2019-03-30 Fixed grounding issue with the force board
    [Force_Sensor_Board.PcbDoc, micro_schematic.SchDoc, power_amp_module.SchDoc]
2019-03-30 Added in an annotation file the last commit didn't catch.
    [Avionics_Sensor_Module.PrjPcb, Force_Sensor_Board.PcbDoc]
2019-03-30 Adding 3D models and DRC
    Added models for the thermocouple connectors and the ceramic resonator in the main board's libraries. Couldn't find a footprint for the thermocouple ICs in any libraries, so holding off on that for now. Also fixed some design rule violations (there were some traces from different nets running over each other near the top left TC connector and I relaxed some of the restrictions on pad/trace proximity (not sure if that's user or project based though - I suck at Altium).
    [rocket_main.PcbDoc]
2019-03-31 Updated TSSOP14 footprint
    Corrected the width of the MAXIM-TSSOP14 footprint for the thermocouple chips and added an outline and pad 1 indicator to it. Rerouted stuff as necessary and also cleaned up some traces coming off the microcontroller with the updated design rule.
    [Temp_converter.SchDoc, rocket_main.PcbDoc, rocket_main.PrjPcb]
2019-03-31 Added TSSOP14 3D Model. Also automatic library removal
    Altium gave me a "PARSEC.[xxx]Lib could not be found and was removed from the project", but it looks like it's still there and everything still seems fine.
    [rocket_main.PcbDoc, rocket_main.PrjPcb]
2019-03-31 TSSOP14 Footprint fix from last commit. Ran DRC
    In the previous commit, I set the origin reference of the TSSOP14 part to "center" and forgot to change it back to its original position. That is fixed now. I also ran DRC and removed some antenna traces (they were just little unconnected stubs) and relaxed some of the rules regarding silkscreen clearances. Not all the rules are resolved, but what's left is probably going to end up being waived, but I want to look through them all anyway. Mostly silk to silk clearance issues in the TC part of the board, but for most of them it's fine if some of the silk gets mushed together.
    [rocket_main.PcbDoc]
2019-04-03 added mounting hole
    added 5th mounting hole (also 6-32) in the middle of the board (x=1.75", y=3.8")
    [rocket_main.PcbDoc]
2019-04-04 Grounded mounting holes. Fixed missing connections
    The mounting holes were grounded because the screws going through them will be going directly into an aluminum box that will shield them from the radio beacon inside the rocket, and that shield needs to be grounded.
    The missing connections I found were two ground pins on the microcontroller and one ground pin on one of the thermocouple ICs that were not connected to ground. Fixed that now.
    [rocket_main.PcbDoc, rocket_main.PrjPcb]
2019-04-05 Added a 3D step file to top directory
    [rocket_main.step]
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2019-04-13 Labelled the CANH and CANL nets appropriately on Force board
    [Force_Sensor_Board.PcbDoc, micro_schematic.SchDoc]
2019-04-13 Shifted traces to make more room around mounting holes on rocket board
    Just making sure that traces don't get squashed by a screw.
    [rocket_main.PcbDoc]
2019-04-14 Enlarged mounting hole size and made room for it
    Mounting holes are now 3/8" diameter. Changed pot pins to 3x1 headers to make room for them, and moved some traces around in the bottom left of the board.
    [rocket_main.PcbDoc]
2019-04-14 Updated step file export
    Now has the 4x1 breakaway debugger pins modelled, and the mounting hole changes.
    [rocket_main.step]
2019-04-15 Silkscreen fixes
    Added Altium logo silkscreen, moved a few labels which were on top of vias for no reason.
    [altiumlogo.PcbDoc, rocket_main.PcbDoc, rocket_main.PrjPcb]
2019-04-15 Updated layer stack
    The PCB layers stack now conforms to the 1.6 mm stackup for JLCPCB, and the stackup files for JLCPCB were added to the top level directory.
    [rocket_main.PcbDoc]
2019-04-16 Ran a final DRC and generated fabrication outputs
    [rocket_main.GBL, rocket_main.GBO, rocket_main.GBS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]
2019-04-16 Added keepout layer and moved comonents in from edge
    Keepout layer provides and outline of the board (needed for fabrication by JLCPCB). This prevents copper from being placed near the edges as well. Thus, I needed to move some things in from the edges and reroute some things accordingly. Fixed DRC violations from this process.
    [rocket_main.PcbDoc]
2019-04-17 Updated fabircation outputs with changes of previous commit
    [rocket_main.GBL, rocket_main.GBS, rocket_main.GKO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]
2019-04-17 Added folder with only files to be sent to JLCPCB for fabrication.
    [rocket_main.GBL, rocket_main.GBO, rocket_main.GBS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]
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2019-04-24 Implemented David and Tyler's final revisions
    Added 45 uF of bulk storage capacitors to LM317s and 15 uF to each valve driver IC to keep the 12V line from dipping when valves draw lots of power.
    Added pull-down resistors to each used enable line for the valve drivers to prevent the line from going high during MCU booting.
    Increased by 10x the resistor values of R6 and R7 (the divider on pressure transducer output) to reduce load on the transducers and be more power efficient.
    Added connector for UART.
    Increased copper pad area and added thermal vias to the LM317 ICs. Complemented this by making the power rails transmitted by copper polygons, for the most part. Also added bottom coppe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
    [Power.SchDoc, Power_Schematic.SchDoc, PressureTransducer.PcbDoc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]
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2019-05-13 finished interface board
    added ignitor connections and cleaned up labels
    [launch_stand_interface.PcbDoc, launch_stand_interface.SchDoc]
2019-05-26 updated interface board for new power supply
    switched from 24pin atx connector to 4pin
    [launch_stand_interface.PcbDoc, launch_stand_interface.PrjPcb, launch_stand_interface.SchDoc]
2019-05-26 Made interface board better suited to high currents
    Replaced backup KK connectors with big pads to solder wires onto. Replaced 12V power traces with polygons, since the 30 mil traces wouldn't be able to handle the expected current draw of all the launch stand boards. Have yet to add some KK connectors to accomodate potential extra boards. The input pads could also have their shape tweaked.
    [launch_stand_interface.PcbDoc, launch_stand_interface.PrjPcb]
2019-05-26 Final edits and fabrication outputs for interface board.
    [PARSEC-LOGO.PcbDoc, altiumlogo.PcbDoc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]
2019-06-17 Corrected labels on ignitor output pins.
    [launch_stand_interface.PcbDoc, launch_stand_interface.PrjPcb]
2019-09-11 Updated CAN configs in pressure code
    CAN bus now runs at 500 kb/s baud with a bit sample point at 86.7%. This should make the bus more tolerant of bit timing errors, which is important with both the beaglebone and stm32s as CAN controllers on the same network
    [can.c]
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2020-01-12 Stuck old code into an archive folder
    [Avionics_Forse_Sensor_Program.ioc, PARSEC_Pressure.ioc, can.c]
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2020-01-23 Preparations for load cell calibration
    Wrote code for calibrating load cells, and got a csv ready and documented for taking data.
    [lm317_10V_2018PCB_load_cell_calibration.csv]
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2020-11-23 Added schematics and parts for in flight data
    Added SMT Microcontroller CAD (schematic and PCB) to Altium library. Also added 3V3 and CAN bus to newly created github project for the in flight data board.
    [CAN_circuit.SchDoc, Power_Schematic.SchDoc, flight_data_rocket_board.PrjPcb]
2020-12-20 Updated libraries with pcb and sch files for FT230XS chip
    *Note: I think I may have accidentally added the pcb file twice to the PARSEC library since the first time I copy/pasted the component it didn't copy anything for some reason. I wasn't sure if I should delete the empty file, so I have left it in the pcb library.
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2021-01-24 Added power bypass capacitors and fixed footprints
    [Power.SchDoc, ValveControl.SchDoc, valvePCB.PcbDoc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]
2021-01-24 Fixed many footprints for valve board
    [CAP_UMA_3X5_NCH.step, Power.SchDoc, ValveControl.SchDoc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]
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2021-02-12 Fixing errors in SPSGRFC schematic
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2021-03-08 Added correct microcontroller and SD module
    [receiver_schematic.SchDoc]
2021-03-09 Fixed ground wiring for valve PCB
    [ValveControl.SchDoc, valvePCB.PcbDoc, valves.SchDoc]
2021-03-22 Prep for Prop Valve Driver Final Review
    Mostly schematic revisions, including adding a reset circuit, adding user input button, adding software controllable LEDs, updating schematic documentation, stylistic improvements, and changing printed designators from physical to logical.
    [Power.SchDoc, ValveControl.SchDoc, buttons.SchDoc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]
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2021-04-09 Julian's final touches on Prop Valve PCB
    Current-carrying polygon tweaking. Improved bypassing on LM317's. Minor shielding. Added power on indicator LED to analog LM317 to meet min. load current, testpoints, final silkscreen.
    [Power.SchDoc, ValveControl.SchDoc, valvePCB.PcbDoc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]
2021-04-09 Added testpoints for current sense amp outputs, swapped around buttons for better labelling, and tuned testpoint holes to fit Keystone THM Multipurpose testpoints.
    [valvePCB.PcbDoc]
2021-04-10 Final valve driver additions
    Mostly just some silkscreen, also enlarged the ceramic resonator.
    [PARSEC-LOGO.PcbDoc, altiumlogo.PcbDoc, penguin_PCB_logo.PcbDoc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]
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2021-04-21 Updated wiring on FT230XS in ground receiver
    Updated wiring, added filter capacitors to microcontroller
    [PARSEC.SchLib, flight_data_sch.SchDoc, receiver_schematic.SchDoc]
2021-04-25 Fixed gerber export of top overlay. Altium 20 had a bug with internal representation of logical designators, so switching to 21 and toggling logical vs physical fixed it. Noted resistor tolerances fo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
    [Power.SchDoc, ValveControl.SchDoc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]
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2021-04-28 Fixed minor issues in flight/ground wireless data boards
    [flight_data_sch.SchDoc, receiver_schematic.SchDoc]
2021-05-17 Fixed pressure sensing code with lpf. Also customized the code for single-sensor operation for a tank proofing test. Originally made as two commits, but a critical file in my .git became corrupted be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
    [main.c, main.h]
2021-05-17 Reverted code back to 9-sensor operation.
    Technically untested, but I think this code will work. A manual effort to detangle a pair of corrupted commits from the previous pool_test commit.
    [can.c, main.c, main.h]
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2021-07-22 fixed net naming
    [valveconn.SchDoc]
2021-07-22 fixed some things
    [beaglebone.SchDoc, hotfire_teststand.PrjPcb, power.SchDoc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]
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2021-10-09 Revert "Merge branch 'master' of https://github.com/Caltech-PARSEC/avionics"
    This reverts commit a2596954eaafc24bad5a41eccdef8835fad8e0b5, reversing
    changes made to e1ef780c82586c8599d901dbf46c97b550534fd8.
    [hotfire_switchboard.PrjPcb, switchboard_misc.PcbLib, top.SchDoc]

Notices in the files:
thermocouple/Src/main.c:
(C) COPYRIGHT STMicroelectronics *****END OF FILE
